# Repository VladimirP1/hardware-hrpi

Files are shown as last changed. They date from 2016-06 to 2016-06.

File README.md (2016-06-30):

# A simple add-on board for Raspberry Pi to run a downstream verion of APM (https://github.com/VladimirP1/ardupilot) (waf configure --board=hrpi)

This board has been designed considering this technology: http://cxem.net/master/45.php

The APM port requires servod form ServoBlaster (https://github.com/richardghirst/PiBits/tree/master/ServoBlaster/user) to be in PATH.

Only one hardware UART is available on the Pi, so either GPS or telemetry should be connected over USB.

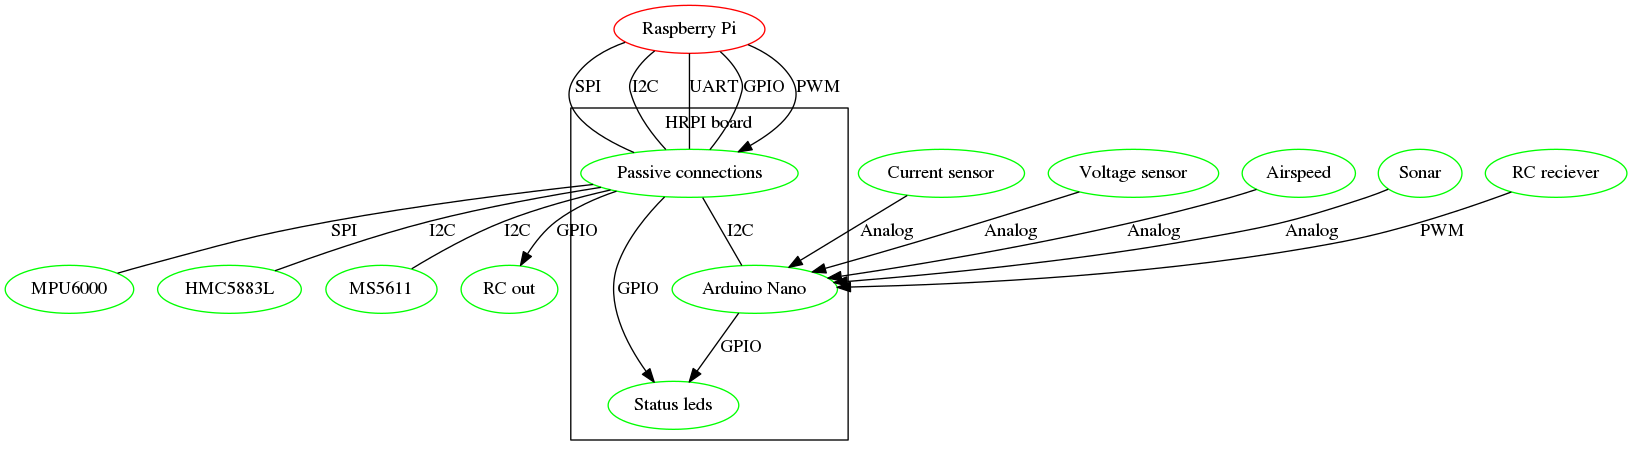
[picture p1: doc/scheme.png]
scheme Diagram


# RT-preempt
- I have built my RT kernel from official Rasberry Pi Foundation's kernel patched with corresponding RT version.
- If your pi does not boot with RT-patched kernel try adding sdhci_bcm2708.enable_llm=0 to cmdline. If you expirince hangs with RT kernel try to add dwc_otg.fiq_enable=0 to cmdline.

# WARNING
-This board uses 10k resistors to protect Raspberry pi's inputs from 5v and relies on its internal protection diodes.
Earlier revision of the board with external diodes work OK, but the current revision is UNTESTED.

-ALWAYS FLASH FIRMWARE BEFORE PLUGGING IN ARDUINO NANO OR YOU RISK TO BURN YOUR PI (It can happen if either of A4 and A5 is driven HIGH) !!!

-Only tested on RPI 2

# Repo structure
- doc: documentation
- src/kicad/hrpi: KICAD sources
- src/arduino/i2c-adc-rc: Arduino sources

# Important notes
- MPU6000 uses MOSI, MISO, SCLK, NSS2, GND, 3V3 form the SPI connector.

# Details
- RC input is recieved by arduino nano, then it is read out by RPI over i2c.
- RC output is done over RPI's gpio using ServoBlaster (https://github.com/richardghirst/PiBits/tree/master/ServoBlaster/user).
- Sensors must be connected externally by SPI and I2C. Madarnatory sensors: MPU6000(SPI), HMC5883L(I2C), MS5611(I2C, except rover).
Examples of breakout boards: GY-63, GY-273 and Mikroe MPU imu click.
- Power must be provided either over the RC rail with P9 closed or the P3 connector

# Serial pinout
serial

# Connecting 3DR radio

If you have two ground modules you can plug one into your PC, one into RPI. They will communicate.
If they do not, make sure that the have same net id.
You can also connect to RPI without 3DR radio, over wifi.

# I2C pinout
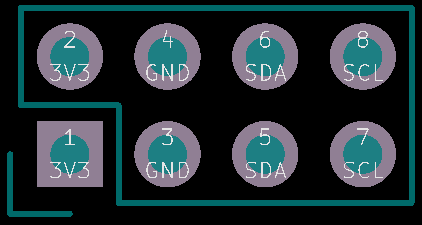
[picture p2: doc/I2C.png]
i2c


# SPI pinout
spi

# How to connect ACC/GYRO
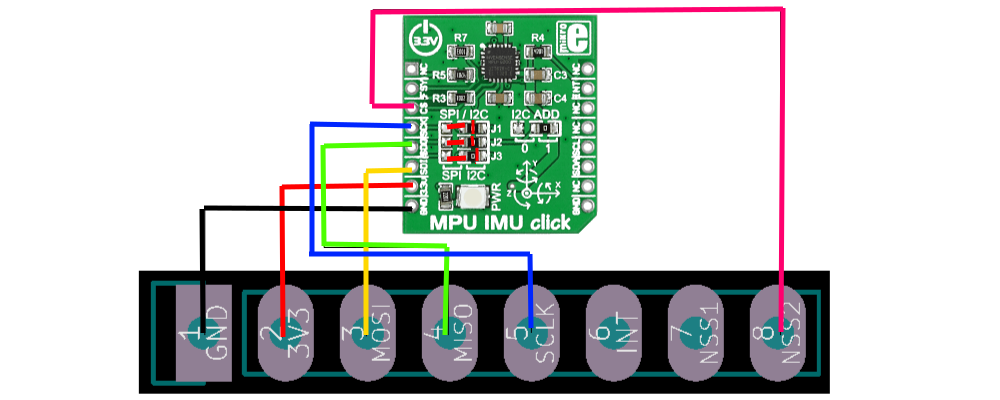
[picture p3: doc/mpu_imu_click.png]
gyroaccel


# ADC pinout
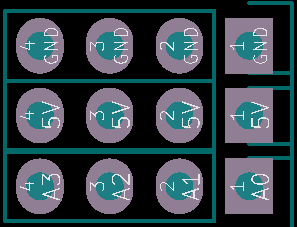
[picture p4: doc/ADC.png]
adc


# RC main pinout
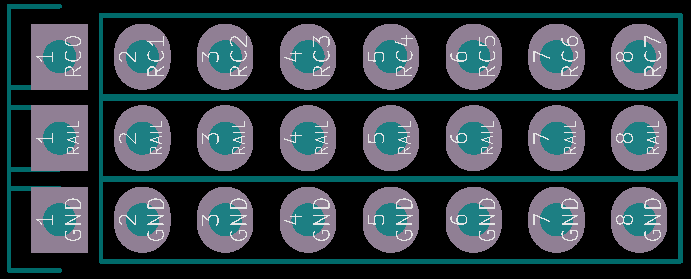
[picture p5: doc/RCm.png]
rcm


# RC aux pinout
AUX0-AUX4=RC8-RC13

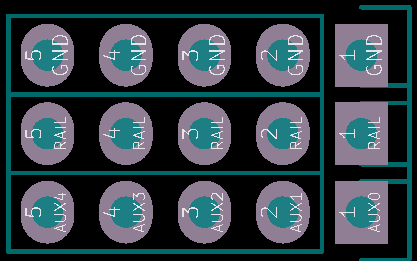
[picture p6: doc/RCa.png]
rca


# Todo
- handle RC OK led by software
- maybe upstream APM
- fix default accel orientation

# Render
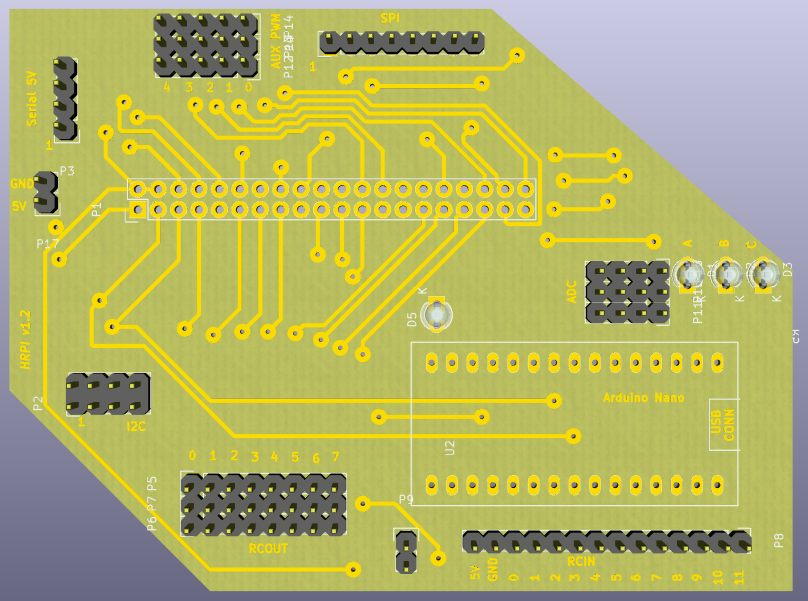
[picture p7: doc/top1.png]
top view HRPI top view

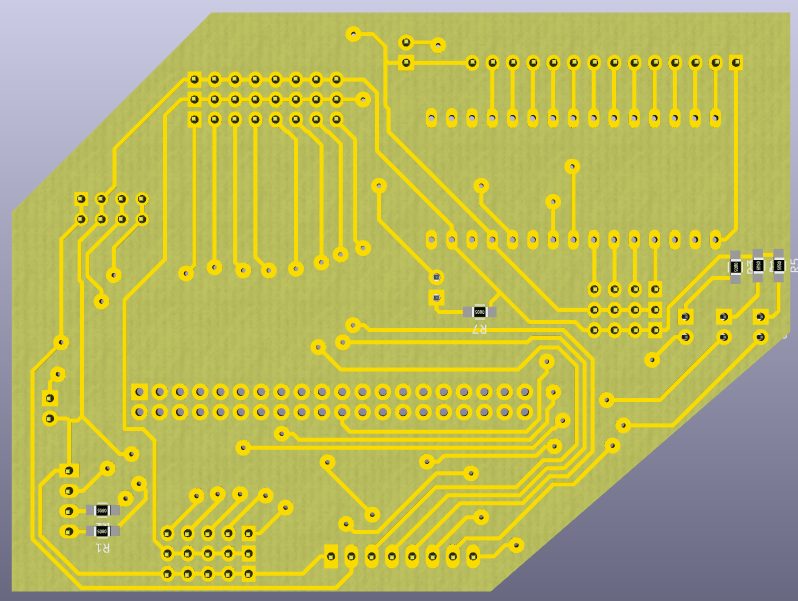
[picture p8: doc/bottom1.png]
bottom view HRPI bottom view


# License
The repo contents are licensed under the MIT license

Copyright (c) 2016 Vladimir Pinchuk

Permission is hereby granted, free of charge, to any person obtaining a copy of this software and associated documentation files (the "Software"), to deal 
in the Software without restriction, including without limitation the rights to use, copy, modify, merge, publish, distribute, sublicense, and/or sell copies of 
the Software, and to permit persons to whom the Software is furnished to do so, subject to the following conditions:

The above copyright notice and this permission notice shall be included in all copies or substantial portions of the Software.

THE SOFTWARE IS PROVIDED "AS IS", WITHOUT WARRANTY OF ANY KIND, EXPRESS OR IMPLIED, INCLUDING BUT NOT LIMITED TO THE WARRANTIES OF MERCHANTABILITY, FITNESS 
FOR A PARTICULAR PURPOSE AND NONINFRINGEMENT. IN NO EVENT SHALL THE AUTHORS OR COPYRIGHT HOLDERS BE LIABLE FOR ANY CLAIM, DAMAGES OR OTHER LIABILITY, WHETHER IN 
AN ACTION OF CONTRACT, TORT OR OTHERWISE, ARISING FROM, OUT OF OR IN CONNECTION WITH THE SOFTWARE OR THE USE OR OTHER DEALINGS IN THE SOFTWARE.

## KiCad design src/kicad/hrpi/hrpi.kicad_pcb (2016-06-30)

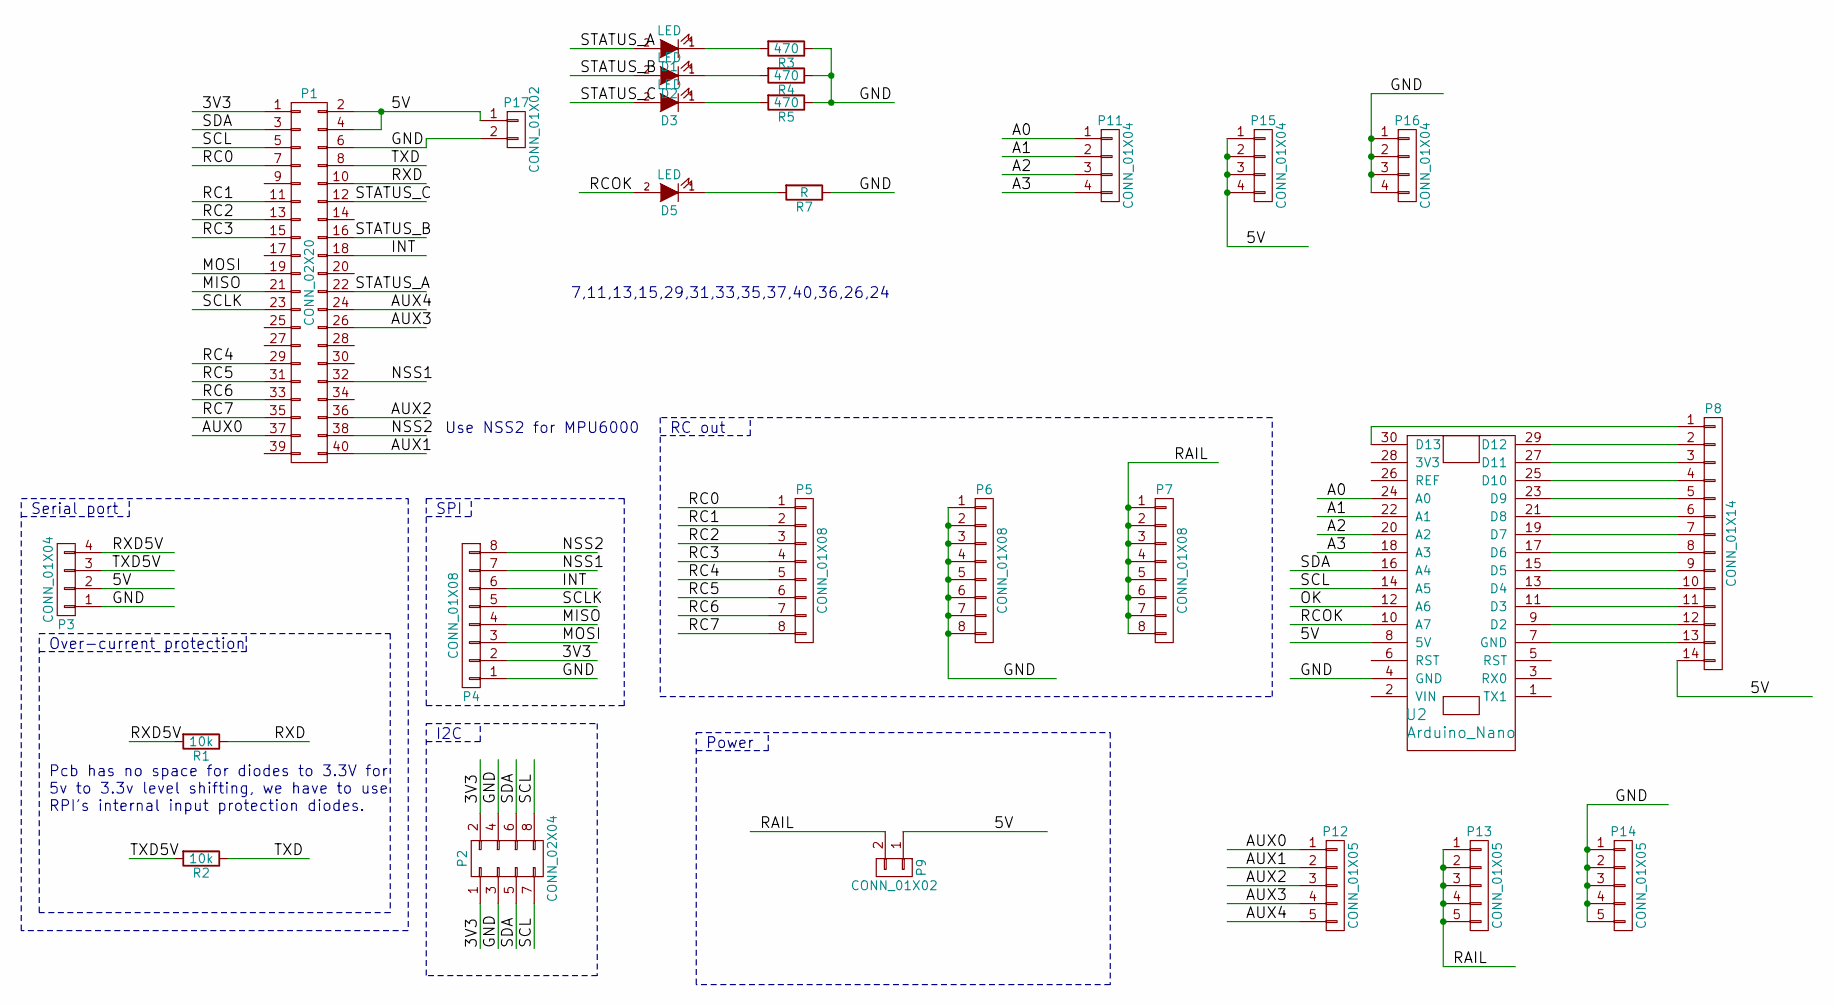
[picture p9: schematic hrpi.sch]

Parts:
D1, D2, D3, D5: LED; LED-3MM
P1: CONN_02X20; Pin_Header_Straight_2x20
P2: CONN_02X04; Pin_Header_Straight_2x04
P3, P11, P15, P16: CONN_01X04; Pin_Header_Straight_1x04
P4, P5, P6, P7: CONN_01X08; Pin_Header_Straight_1x08
P8: CONN_01X14; Pin_Header_Straight_1x14
P9, P17: CONN_01X02; Pin_Header_Straight_1x02
P12, P13, P14: CONN_01X05; Pin_Header_Straight_1x05
R1, R2: 10k; R_0805_HandSoldering
R3, R4, R5: 470; R_0805_HandSoldering
R7: R; R_0805_HandSoldering
U2: Arduino_Nano; arduino_nano

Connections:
/3V3: P1.1, P2.1, P2.2, P4.2
/5V: P1.2, P1.4, P3.2, P8.14, P9.1, P15.1, P15.2, P15.3, P15.4, P17.1, U2.8 (5V)
/A0: P11.1, U2.24 (A0)
/A1: P11.2, U2.22 (A1)
/A2: P11.3, U2.20 (A2)
/A3: P11.4, U2.18 (A3)
/AUX0: P1.37, P12.1
/AUX1: P1.40, P12.2
/AUX2: P1.36, P12.3
/AUX3: P1.26, P12.4
/AUX4: P1.24, P12.5
/GND: P1.6, P2.3, P2.4, P3.1, P4.1, P6.1, P6.2, P6.3, P6.4, P6.5, P6.6, P6.7, P6.8, P14.1, P14.2, P14.3, P14.4, P14.5, P16.1, P16.2, P16.3, P16.4, P17.2, R3.1, R4.1, R5.1, R7.1, U2.4 (GND)
/INT: P1.18, P4.6
/MISO: P1.21, P4.4
/MOSI: P1.19, P4.3
/NSS1: P1.32, P4.7
/NSS2: P1.38, P4.8
/RAIL: P7.1, P7.2, P7.3, P7.4, P7.5, P7.6, P7.7, P7.8, P9.2, P13.1, P13.2, P13.3, P13.4, P13.5
/RC0: P1.7, P5.1
/RC1: P1.11, P5.2
/RC2: P1.13, P5.3
/RC3: P1.15, P5.4
/RC4: P1.29, P5.5
/RC5: P1.31, P5.6
/RC6: P1.33, P5.7
/RC7: P1.35, P5.8
/RCOK: D5.2 (A), U2.10 (A7)
/RXD: P1.10, R1.1
/RXD5V: P3.4, R1.2
/SCL: P1.5, P2.7, P2.8, U2.14 (A5)
/SCLK: P1.23, P4.5
/SDA: P1.3, P2.5, P2.6, U2.16 (A4)
/STATUS_A: D1.2 (A), P1.22
/STATUS_B: D2.2 (A), P1.16
/STATUS_C: D3.2 (A), P1.12
/TXD: P1.8, R2.1
/TXD5V: P3.3, R2.2
unnamed: D1.1 (K), R3.2
unnamed: D2.1 (K), R4.2
unnamed: D3.1 (K), R5.2
unnamed: D5.1 (K), R7.2
unnamed: P8.1, U2.30 (D13)
unnamed: P8.2, U2.29 (D12)
unnamed: P8.3, U2.27 (D11)
unnamed: P8.4, U2.25 (D10)
unnamed: P8.5, U2.23 (D9)
unnamed: P8.6, U2.21 (D8)
unnamed: P8.7, U2.19 (D7)
unnamed: P8.8, U2.17 (D6)
unnamed: P8.9, U2.15 (D5)
unnamed: P8.10, U2.13 (D4)
unnamed: P8.11, U2.11 (D3)
unnamed: P8.12, U2.9 (D2)
unnamed: P8.13, U2.7 (GND)

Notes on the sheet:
Over-current protection
Serial port
I2C
SPI
Use NSS2 for MPU6000
RC out
Power
Pcb has no space for diodes to 3.3V for 5v to 3.3v level shifting, we have to use RPI's internal input protection diodes.
7,11,13,15,29,31,33,35,37,40,36,26,24

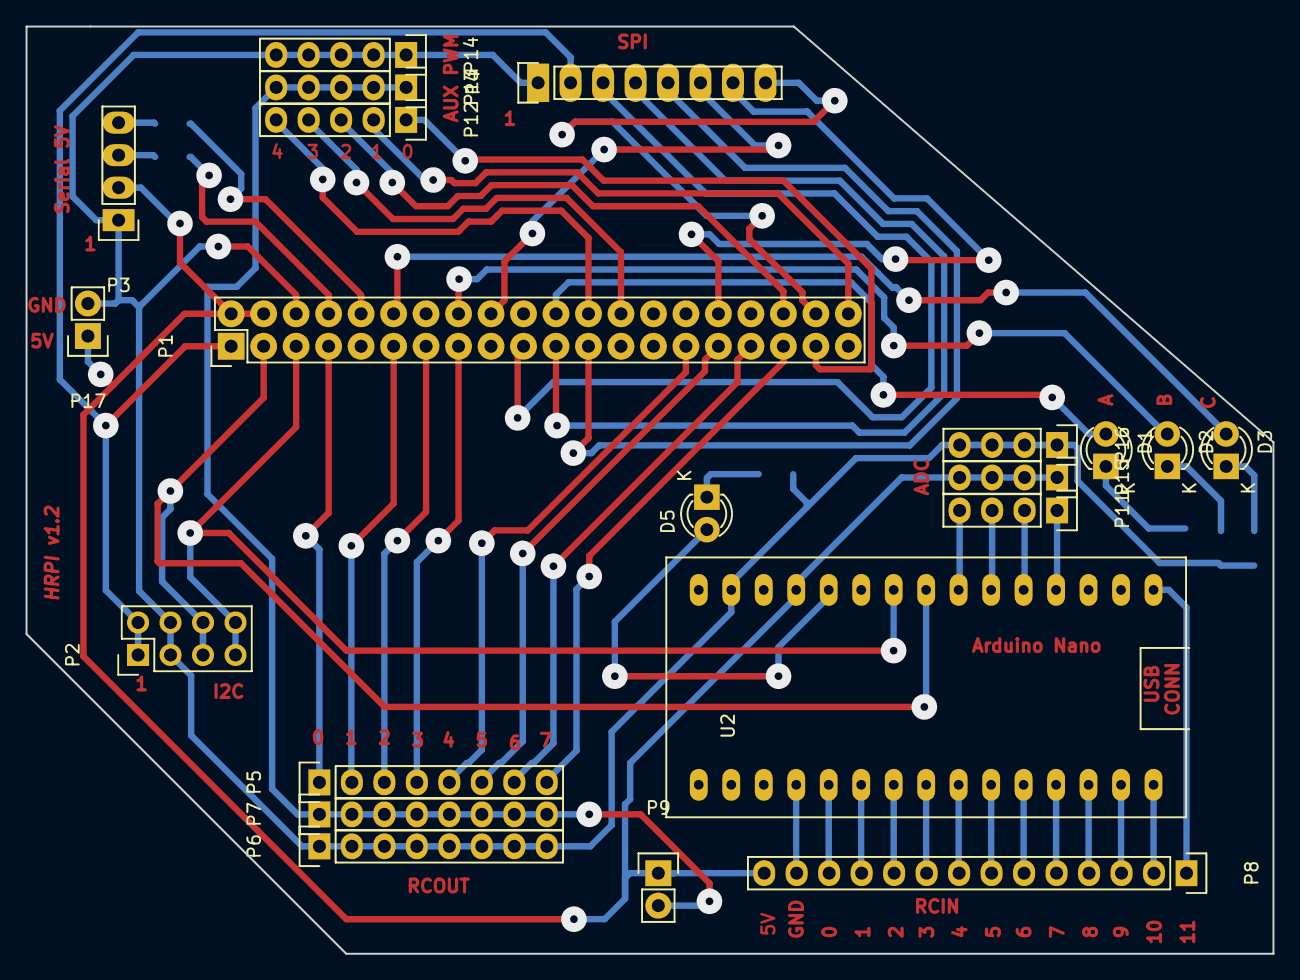
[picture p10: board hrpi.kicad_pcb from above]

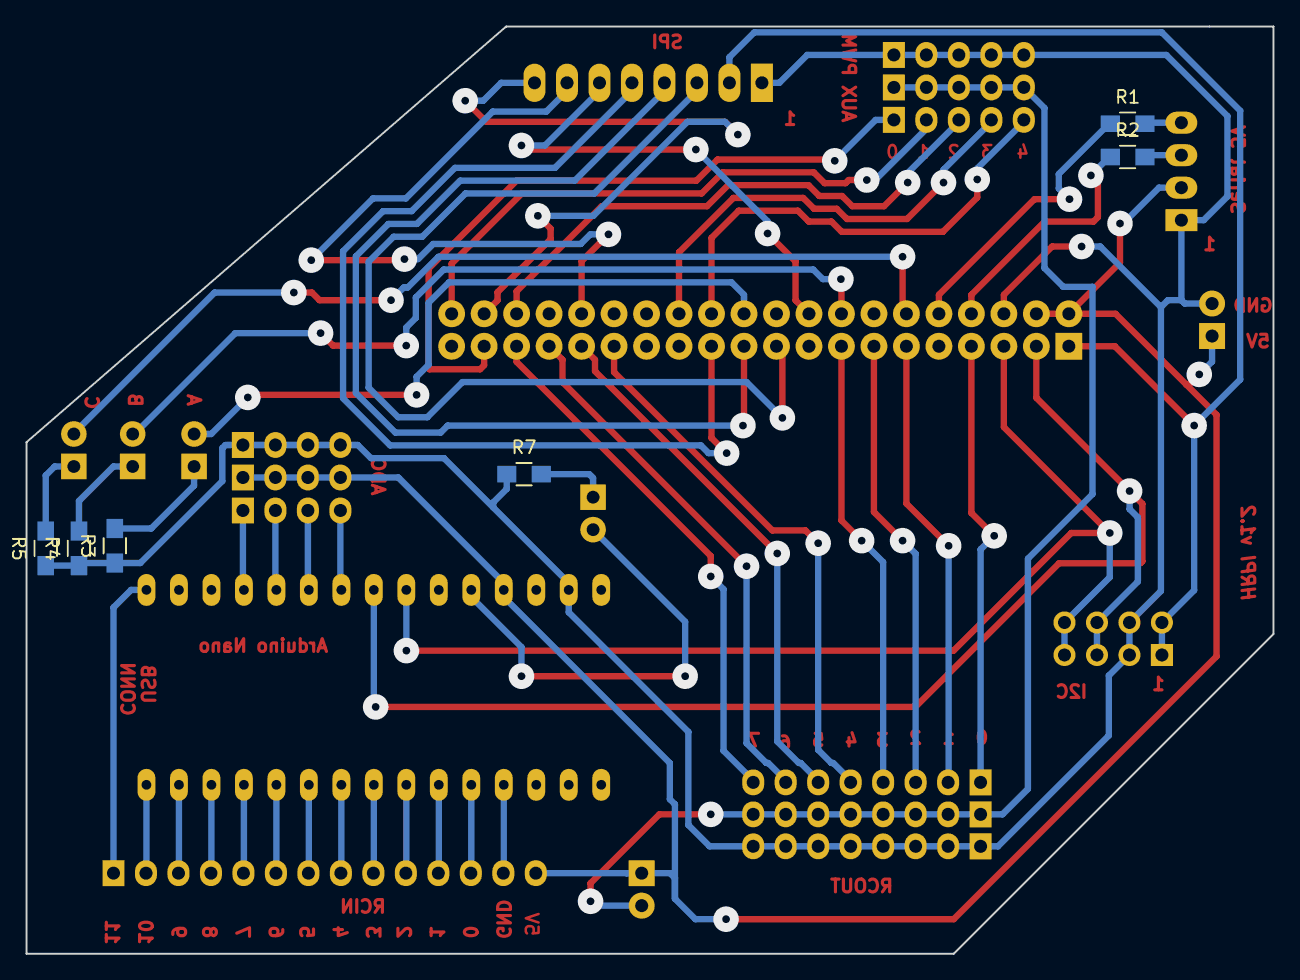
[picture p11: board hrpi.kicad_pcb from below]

Board: 2 copper layers, 97.5 x 72.5 mm, 27 parts (6 on the bottom side), 54 nets.

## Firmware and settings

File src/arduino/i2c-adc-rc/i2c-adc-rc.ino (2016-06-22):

//Register map:
// 0  ID 0x43
// 1  A0:LSB
// 2  A0:MSB
// 3  A1:LSB
// 4  A1:MSB
// 5  A2:LSB
// 6  A2:MSB
// 7  A3:LSB
// 8  A3:MSB
// 9  ADCR: | RES | RES | RES | RES | ADC3| ADC2| ADC1| ADC0|
// A  RC1 :LSB
// B  RC1 :MSB
// C  RC2 :LSB
// D  RC2 :MSB
// E  RC3 :LSB
// F  RC3 :MSB
// 10 RC4 :LSB
// 11 RC4 :MSB
// 12 RC5 :LSB
// 13 RC5 :MSB
// 14 RC6 :LSB
// 15 RC6 :MSB
// 16 RC7 :LSB
// 17 RC7 :MSB
// 18 RC8 :LSB
// 19 RC8 :MSB
// 20 RC8 :LSB
// 21 RC9 :MSB
// 22 RC9 :LSB
// 23 RC10:MSB
// 24 RC10:LSB
// 25 RC11:MSB
// 26 RC12:LSB
// 27 RC12:MSB

#include <Wire.h>

volatile unsigned char ret = 0;
volatile unsigned char regs[0x28];
volatile unsigned char regs1[0x28];

#define NREGS 0x20

void setup() {
  regs[0] = 0x43;
  for (int i = 1; i < NREGS; i++)
    regs[i] = 0;
  for (int i = 1; i < NREGS; i++)
    regs1[i] = 0;
  Serial.begin(9600);
  Wire.begin(8);
  PORTC &= ~(1 << 5);
  PORTC &= ~(1 << 4);
  Wire.onReceive(receiveEvent);
  Wire.onRequest(requestEvent);
  setuppcint();
  //ppm_init();
}

void loop() {
  unsigned int a;
  if (regs[9] & (1 << 0)) {
    //Serial.println("ADC1");
    a = 0;
    analogRead(A0);
    delay(10);
    a = analogRead(A0);
    a += analogRead(A0);
    a += analogRead(A0);
    a += analogRead(A0);
    a = a / 4;
    regs1[1] = a & 0xff;
    regs1[2] = (a >> 8) & 0xff;
  }
  if (regs[9] & (1 << 1)) {
    //Serial.println("ADC2");
    analogRead(A1);
    delay(10);
    a = analogRead(A1);
    a += analogRead(A1);
    a += analogRead(A1);
    a += analogRead(A1);
    a = a / 4;
    regs1[3] = a & 0xff;
    regs1[4] = (a >> 8) & 0xff;
  }
  if (regs[9] & (1 << 2)) {
    //Serial.println("ADC3");
    analogRead(A2);
    delay(10);
    a = analogRead(A2);
    a += analogRead(A2);
    a += analogRead(A2);
    a += analogRead(A2);
    a = a / 4;

    regs1[5] = a & 0xff;
    regs1[6] = (a >> 8) & 0xff;
  }
  if (regs[9] & (1 << 3)) {
    //Serial.println("ADC4");
    analogRead(A3);
    delay(10);
    a = analogRead(A3);
    a += analogRead(A3);
    a += analogRead(A3);
    a += analogRead(A3);
    a = a / 4;
    regs1[7] = a & 0xff;
    regs1[8] = (a >> 8) & 0xff;
  }
  /*uint8_t a1=TCNT2;
    delayMicroseconds(8);
    uint8_t a2=TCNT2;
    Serial.print(a1);
    Serial.print("\t");
    Serial.print(a2);
    Serial.print("\t");
    Serial.println((uint8_t)(a2-a1));*/
  //Serial.println(regs[0xa + (2 * 2)]);
  //delay(100);

  /*for (int i = 0; i < NREGS; i++) {
    Serial.print(i, HEX);
    Serial.print("\t");
    Serial.println(regs[i], HEX);
    }
    Serial.println("-----------------------------------------");
    delay(1000);*/
}

void requestEvent()
{
  Wire.write(ret);
}
void receiveEvent(int nbytes) {
  unsigned char x = Wire.read();
  if (nbytes == 1) {
    if (x < NREGS)
      ret = regs[x];
    else
      ret = 0x23;
    if (x == 0x27/*0x19*/)
      for (int i = 0; i < 24; i++)
        regs[i + 0xA] = regs1[i + 0xA];
    else if (x == 0x8)
      for (int i = 0; i < 8; i++)
        regs[i + 0x1] = regs1[i + 0x1];
  } else if (nbytes == 2) {
    while (!Wire.available() > 0);
    int n = Wire.read();
    if (x > 0 && x < NREGS)
      regs[x] = n;
  } else {
    ret = 0x23;

  }
  while (Wire.read() >= 0);
}

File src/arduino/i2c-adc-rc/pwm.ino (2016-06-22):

volatile boolean states[12];
volatile uint16_t last[12];
volatile uint8_t nchan;
volatile boolean dir;
#define MICROS_PER_TICK 8
//CH0  D2  PD2 PCINT18
//CH1  D3  PD3 PCINT19
//CH2  D4  PD4 PCINT20

//CH3  D5  PD5 PCINT21
//CH4  D6  PD6 PCINT22
//CH5  D7  PD7 PCINT23

//CH6  D8  PB0 PCINT0
//CH7  D9  PB1 PCINT1
//CH8  D10 PB2 PCINT2
//CH9  D11 PB3 PCINT3
//CH10 D12 PB4 PCINT4

//CH11 D13 PB5 PCINT5

//PCMSK0  0-7
//PCMSK1  8-15
//PCMSK2  16-23

void setuppcint() {
  DDRD &= ~(1 << 3);
  DDRD &= ~(1 << 4);
  DDRD &= ~(1 << 2);
  DDRD &= ~(1 << 5);//0 P2
  DDRD &= ~(1 << 6);//1 P2
  DDRD &= ~(1 << 7);//2 P2
  DDRB &= ~(1 << 0);//3 P0
  DDRB &= ~(1 << 1);//4 P0
  DDRB &= ~(1 << 2);//5 P0
  DDRB &= ~(1 << 3);//6 P0
  DDRB &= ~(1 << 4);//7 P0
  DDRB &= ~(1 << 5);

  DDRB |= (1 << 5);
  PCICR |= (1 << PCIE0) | (1 << PCIE1) | (1 << PCIE2);
  PCMSK0 |= (1 << PCINT0) | (1 << PCINT1) | (1 << PCINT2) | (1 << PCINT3) | (1 << PCINT4);
  PCMSK2 |= (1 << PCINT21) | (1 << PCINT22) | (1 << PCINT23);
  TCCR1A = 0;
  TCCR1B = (1 << CS11);
}


ISR(PCINT0_vect) {
  uint16_t l = TCNT1;
  if ((PINB & (1 << 0)) != states[6]) {
    states[6] = PINB & (1 << 0);
    nchan = 6;
    dir = PINB & (1 << 0);
  }
  else if ((PINB & (1 << 1)) != states[7]) {
    states[7] = PINB & (1 << 1);
    nchan = 7;
    dir = PINB & (1 << 1);
  }  else if ((PINB & (1 << 2)) != states[8]) {
    states[8] = PINB & (1 << 2);
    nchan = 8;
    dir = PINB & (1 << 2);
  }  else if ((PINB & (1 << 3)) != states[9]) {
    states[9] = PINB & (1 << 3);
    nchan = 9;
    dir = PINB & (1 << 3);
  }
  else if ((PINB & (1 << 4)) != states[10]) {
    states[10] = PINB & (1 << 4);
    nchan = 10;
    dir = PINB & (1 << 4);
  }
  else if ((PINB & (1 << 5)) != states[11]) {
    states[11] = PINB & (1 << 5);
    nchan = 11;
    dir = PINB & (1 << 5);
  }
  else {
    return;
  }

  if (dir) {
    last[nchan] = l;
  } else {
    uint16_t diff = (uint16_t)(l - last[nchan]);
    diff = diff >> 1;
    regs1[0xA + (nchan * 2)] = diff & 0xff;
    regs1[0xB + (nchan * 2)] = (diff >> 8) & 0xff;
  }

}
ISR(PCINT2_vect) {
  uint16_t l = TCNT1;
  if ((PIND & (1 << 2)) != states[0]) {
    states[0] = PIND & (1 << 2);
    nchan = 0;
    dir = PIND & (1 << 2);
  }
  else if ((PIND & (1 << 3)) != states[1]) {
    states[1] = PIND & (1 << 3);
    nchan = 1;
    dir = PIND & (1 << 3);
  }
  else if ((PIND & (1 << 4)) != states[2]) {
    states[2] = PIND & (1 << 4);
    nchan = 2;
    dir = PIND & (1 << 4);
  }
  else if ((PIND & (1 << 5)) != states[3]) {
    states[3] = PIND & (1 << 5);
    nchan = 3;
    dir = PIND & (1 << 5);
  }
  else if ((PIND & (1 << 6)) != states[4]) {
    states[4] = PIND & (1 << 6);
    nchan = 4;
    dir = PIND & (1 << 6);
  }
  else if ((PIND & (1 << 7)) != states[5]) {
    states[5] = PIND & (1 << 7);
    nchan = 5;
    dir = PIND & (1 << 7);
  }
  else {
    return;
  }

  if (dir) {
    last[nchan] = l;
  } else {
    uint16_t diff = (uint16_t)(l - last[nchan]);
    diff = diff >> 1;
    regs1[0xA + (nchan * 2)] = diff & 0xff;
    regs1[0xB + (nchan * 2)] = (diff >> 8) & 0xff;
  }
}

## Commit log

2016-06-20 Initial commit of HRPI design files.
    [test.kicad_pcb, test.sch]
2016-06-21 Move submodule to main repo
    [_saved_test.sch]
2016-06-21 Input channel count increased in hardware, but not in software
    [_saved_test.sch, test.kicad_pcb, test.sch]
2016-06-21 Status leds added to hardware
    [test.kicad_pcb, test.sch]
2016-06-21 Bugs fixed, added 5v connector
    [test.kicad_pcb, test.sch]
2016-06-22 Added board render
    [test.kicad_pcb, test.sch]
2016-06-22 Files reordered
    [test.kicad_pcb, test.sch]
2016-06-22 Added 12 channel untested pwm to i2c encoder code
2016-06-30 Replaced power jumper
    [hrpi.kicad_pcb, hrpi.sch]
2016-06-30 Some traces moved
    [hrpi.kicad_pcb]
